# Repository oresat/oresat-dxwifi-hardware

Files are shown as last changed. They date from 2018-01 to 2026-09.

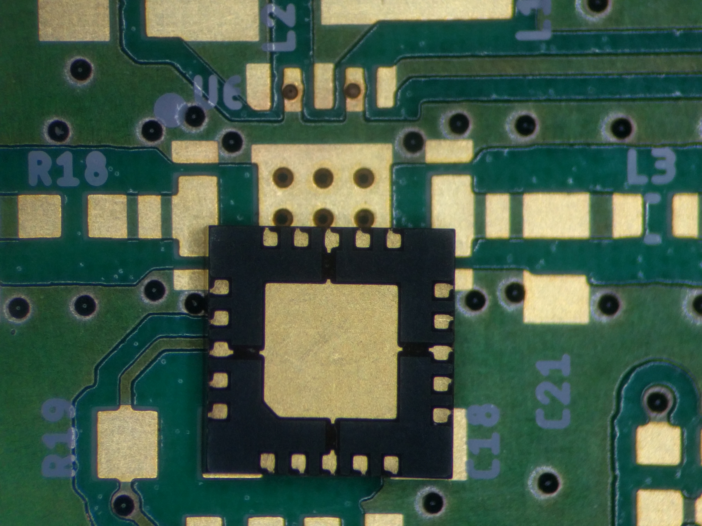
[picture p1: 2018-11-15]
bi-directional-amp-board_V2/v1_notes/IMG_20181114_184748.jpg

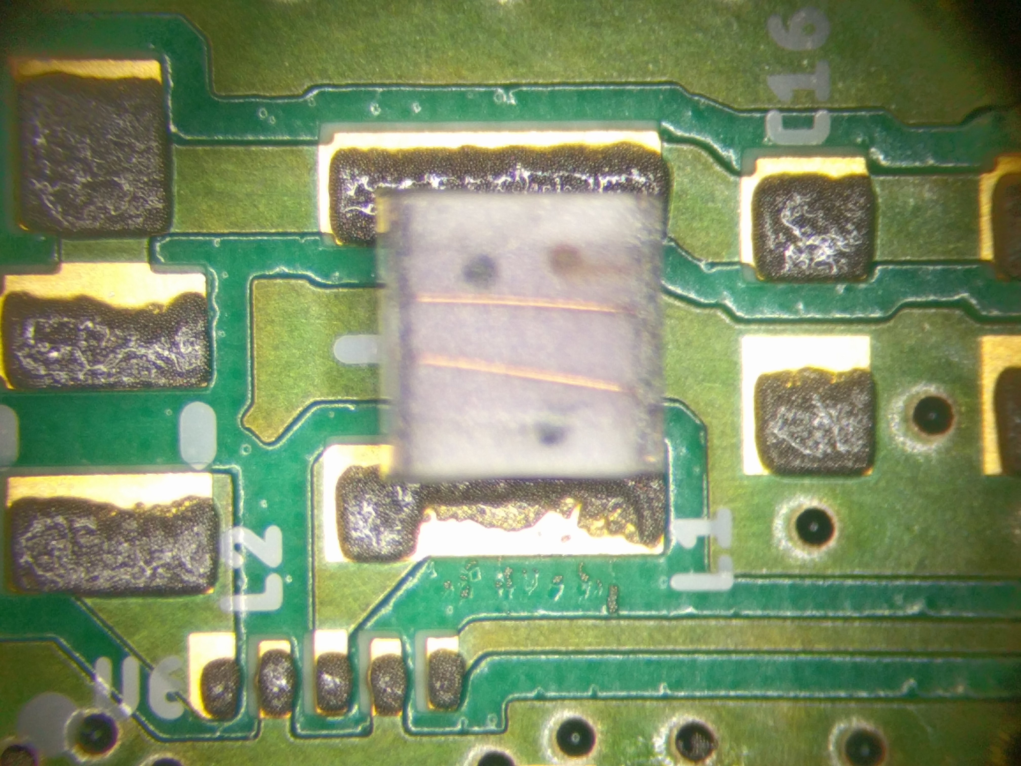
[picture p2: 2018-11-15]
bi-directional-amp-board_V2/v1_notes/IMG_20181114_191043.jpg

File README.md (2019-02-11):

# oresat-dxwifi-hardware
This repository is for the DxWiFi hardware that will fly on the OreSat satellite. DxWiFi is our communication subsystem for high speed data (1 Mbps) using 2.4 GHz WiFi between the spacecraft and ground.

This is hardware for the **satellite** only; please see the other repos if you're looking for the [OreSat Live Handheld Ground Station](https://github.com/oresat/oresat-live-handheld-ground-station) or the [Mini-OreSat testing platform for high altitude balloons](https://github.com/oresat/oresat-live-mini-oresat).

We intend to use "ordinary WiFi" (IEEE 802.11b) as a high speed satellite communication system. What is _not_ ordinary is that we run the radio under the amateur radio rules and regulations (FCC Part 97) and thus can increase power levels and antenna gains necessary to make the link budget work.

### Ordinary WiFi
The plan is to use the Qualcomm Atheros AR9271 USB to WiFi adapter because of the driver support in Linux.

### Non ordinary bi-directional power amplifier
This project is intended to operate under the Amateur Radio Service [47CFR97](https://www.gpo.gov/fdsys/pkg/CFR-1996-title47-vol5/pdf/CFR-1996-title47-vol5-part97.pdf) whereby larger power levels and higher gain directional antennas can be used within the [13 cm band](https://en.wikipedia.org/wiki/13-centimeter_band) to close the link.

NB:  There are other DxWiFi materials on the PSAS GitHub repo, but those repos are deprecated.

Link budgets can be found [here](https://github.com/oresat/oresat-dxwifi-hardware/tree/master/Link-Model).

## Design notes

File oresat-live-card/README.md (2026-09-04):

---
title: "**OreSat Live / DxWiFi Card**"
subtitle: |
  **Fabrication and Assembly Information**\
  For build TIME-STAMP
fontsize: 10pt
geometry:
  - margin=0.5in
toc: true
toc-depth: 2
colorlinks: true
urlcolor: blue
---

\newpage

# About this Board

## Board Description

TODO: DESCRIBE CARD

## Documentation Links

- OL hardware Git repository: <https://github.com/oresat/oresat-dxwifi-hardware>
- OL software Git reposity: <https://github.com/oresat/oresat-dxwifi-software>
- **TODO:** OL Design Notes + Design Review Notes

## Documentation Files

| Filename | Notes |
| --- | --- |
| README.pdf | This README file |
| PROJECT-NAME-outline.dxf | Board outline (with holes) in DXF format |
| PROJECT-NAME-pcba.step | 3D model of PCBA (with components) |
| PROJECT-NAME-render-bot.jpg | Render of the top of the 3D model |
| PROJECT-NAME-render-bot.jpg | Render of the bottom of the 3D model |
| PROJECT-NAME-schematic.pdf | PDF of board schematics |

## Contact Information

- Website: <https://www.oresat.org/>
- Email: <oresat@pdx.edu>
- Instagram: @pdxaerospace

## Board Renders

Render of the top of the 3D model
Render of the bottom of the 3D model

\newpage

# Printed Circuit Board (PCB) Fabrication Information

## Board Info

- 4 layer board
- Bounding box is 99.8 x 94.6 mm (3.93 x 3.72 in)
- Board thickness is 1.59 mm (0.063 inch)
- **Important:** See Materials and Stack Up sections below

## Board Requirements

- Design Rules
    - Minimum Trace / Space design rules
       - Outer layers: 0.127 mm (5.0 mil) / 0.127 mm (5.0 mil)
       - Inner layers: 0.127 mm (5.0 mil) / 0.127 mm (5.0 mil)
    - Outer dimension router tolerance: +/- 0.254 mm (10.0 mil)
    - Hole placement tolerance: +/- 0.075 mm (3.0 mil)
    - Inner tab routed slot tolerance: +/- 0.254 mm (10.0 mil)
- Drills
   - Drill Positional Tolerance: 0.051 mm (2.0 mil)
   - Drill Size tolerance: +/- 0.064 mm (2.5 mil)
- Plated/Un-plated holes
  - There are 6 un-plated (NPT) holes
  - There are 1477 plated through (PTH) holes
  - PTH minimum diameter: 0.254 mm (10 mil)
  - PTH minimum annulus: 0.102 mm (4 mil) radius
- Outline/Routing
  - Requires a 1.0 mm or smaller diameter routing bit
- Slots
  - There are no slots.
- Cutouts
  - There are no cutouts
- There are 3 fiducials on the top layer and 3 on the bottom layer.
- Panel tabs ("mouse bites")
   - Card edges must be smooth; no mouse bites or other intrusions into the card outline.
   - If external mouse bites are required, minimize and customer will remove by hand before assembly.
- If not otherwise specified, build to IPC 6012 Class 2 or better.

## Materials

- Controlled impedance
   - The stackup is critical for the performance of high speed signals on this board.
   - As long as the stackup is controlled, the board is not considered controlled impedance.
- Isola FR408HR or material with equivalent Dk.
- Board Surface treatment should be ENIG, althogh immersion Silver is acceptable.
- White silkscreen on top and bottom surface
- Taiyo PSR-4000 or equivalent soldermask on top and bottom, no requirements for color.

## Stack Up

| Layer | Thickness | Notes |
|---|---|---|
| Top Copper | 0.043 mm /  1.7 mil |  Layer 1 foil, 1 oz Cu after plating |
| prepreg | 0.200 mm /  7.9 mil |  Prepreg - Isola FR408HR 2113 |
| Layer 2 | 0.018 mm /  0.7 mil |  Layer 2 foil, 0.5 oz Cu |
| Core | 0.991 mm / 39 mil |  Core Isola FR408HR |
| Layer 3 | 0.018 mm /  0.7 mil |  Layer 3 foil, 0.5 oz Cu |
| prepreg | 0.200 mm /  7.9 mil |  Prepreg - Isola FR408HR 2113 |
| Bottom Copper | 0.043 mm /  1.7 mil |  Layer 4 foil, 1 oz copper after plating |
| **Total Stackup** | **1.588 mm / 62.5 mil** | |

## Array / Panel Information

- Coordinate with Contract Manufacturer (CM) for optimal size of this panel.
- If no feedback from CM, then produce single boards (no panel).

## Fabrication Files

### IPC-2581 File

| Filename | Notes |
| --- | --- |
| PROJECT-NAME-ipc2581.xml | IPC-2581 board information file |

### Legacy PCB Files

| Filename | Notes |
| ---| --- |
| PROJECT-NAME-Edge_Cuts.gbr | RS274X file for the dimension (outline) layer |
| PROJECT-NAME-F_Silkscreen.gbr | RS274X file for the top silkscreen |
| PROJECT-NAME-F_Mask.gbr | RS274X file for the top soldermask |
| PROJECT-NAME-F_Cu.gbr | RS274X file for the top copper layer |
| PROJECT-NAME-In1_Cu.gbr | RS274X file for the layer 2 copper |
| PROJECT-NAME-In2_Cu.gbr | RS274X file for the layer 3 copper |
| PROJECT-NAME-B_Cu.gbr | RS274X file for the bottom copper layer |
| PROJECT-NAME-B_Mask.gbr | RS274X file for the bottom soldermask |
| PROJECT-NAME-B_Silkscreen.gbr | RS274X file for the bottom silkscreen |
| PROJECT-NAME-NPTH.drl | Excellon file for non-plated through holes |
| PROJECT-NAME-PTH.drl | Excellon file for plated through holes | 

\newpage

# Printed Circuit Board Assembly (PCBA) Information

## Assembly Info

- There are components are on the top and bottom side of the board.
- This PCBA is mostly surface mount (SMT) with a few (THT) components.

## Assembly Requirements

- Assemble to IPC Class 2 or better
- Bake components that are not moisture sealed to appropriate levels as required.
- Solder paste MUST be leaded.
- Aqueous flux and wash strongly preferred.
   - Clean to NASA Standard "Visibly Clean (VC)": No particles or residues are visible to the naked eye.
- No conformal coating.
- Ship in antistatic protective bag

## Component Specific Assembly Information

- SMPM connectors (J3, J4) should be hand-added according to the Oresat SOP.

## Assembly Files

### IPC-2581 File

| Filename | Notes |
| --- | --- |
| PROJECT-NAME-ipc2581.xml | IPC-2581 board information file |

### Bill of Materials (BOM)

| Filename | Description |
| --- | --- |
| PROJECT-NAME-bom.csv | BOM in Comma Separated Variable format |

### Solder Paste Stencils

| Filename | Notes |
| --- | --- |
| PROJECT-NAME-B_Paste.gbr | RS274X file for top/front solder paste stencil |
| PROJECT-NAME-F_Paste.gbr | RS274X file for bottom/back solder paste stencil |

### Mounting/Placement Location

| Filename | Description |
| --- | --- |
| PROJECT-NAME-3u.pos | Pick and place locations for components |

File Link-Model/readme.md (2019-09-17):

### Link Budget Models for the DxWiFi Channel

The source of these link model spreadsheets are from Jan King and are located at the [AMSAT-UK IARU website](http://www.amsatuk.me.uk/iaru/spreadsheet.htm).  The spreadsheets have been customized from revision 2.5.5 which are signified by a suffix letter.  In addition, for OreSat protocol information please visit our [GitHub protocol page](https://github.com/oresat/oresat-design/tree/gh-pages/protocol).  For OreSat's primary communication link models please visit our [GitHub C3 RF page](https://github.com/oresat/oresat-c3-rf/link-models)

* The bulk-data mission uplink and downlink using UniClOGS (University Class Open Ground Station)
  * ___OreSat1_link_model_v2.5.5a_mission_data_uniclogs.xlsx  (PDF summary)___
  * S band - 2422 MHz - 1Mbps 802.11b
  * 45 deg minimum elevation
  * 1.4 dBi canted turnstile on satellite and 23 dBi parabolic reflector at ground station for uplink
  * 12 dBi helix on satellite and 23 dBi parabolic reflector at ground station for downlink

* The bulk-data mission downlink using a handheld ground station receiver
  * ___OreSat1_link_model_v2.5.5a_mission_data_handheld.xlsx  (PDF summary)___
  * S band - 2422 MHz - 1Mbps 802.11b
  * 45 deg minimum elevation
  * 12 dBi helix on satellite and 15 dBi quad helix/patch at ground station

Notes:
- The 'Transmitters' and 'Receivers' sheets have been customized
  - Block diagrams reflect correct design
  - System noise temperature is more precise
- The 'System Performance Summary' sheet has been customized
  - Power levels in dBm
  - More link details

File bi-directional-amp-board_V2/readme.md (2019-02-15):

Notes on the Bi-Directional DxWiFi (2.412 GHz) Amp PCB
========================================================

Our stackup is something like this:

 1.2 mil - 1 oz Copper
13.3 mil - Rogers RO4350B
 1.2 mil - 1 oz Copper
31.1 mil - FR4 (e.g., NP175)
 1.2 mil - 1 oz Copper
13.3 mil - Rogers RO4350B
 1.2 mil - 1 oz Copper
--------
62.5 mil - 1/16" standard board thickness

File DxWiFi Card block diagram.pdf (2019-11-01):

To Helix
Antenna

To Turnstile
Antenna

WiFi Adapter
TX Port

WiFi Adapter
RX Port

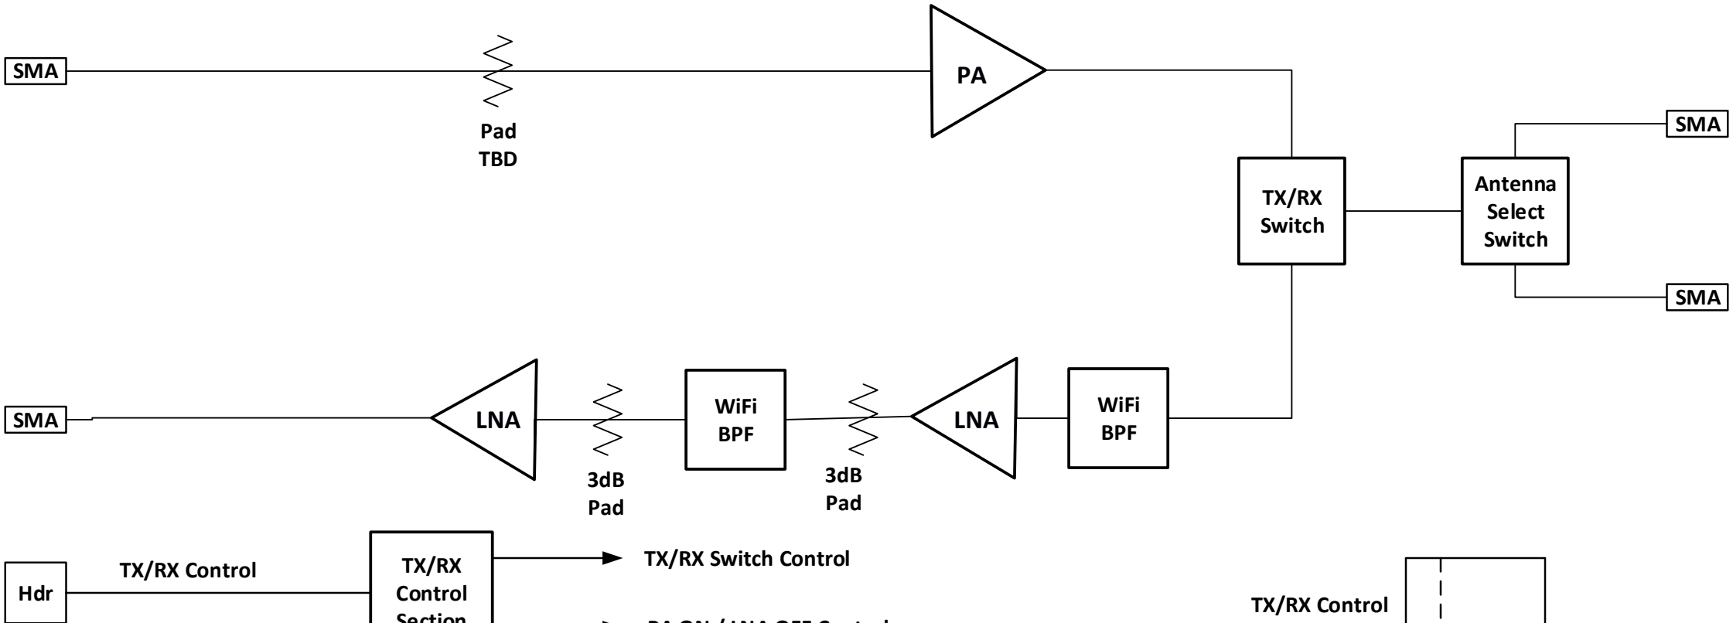
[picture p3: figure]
TX/RX Switch; Antenna Select Switch; WiFi BPF; WiFi; BPF LNA; LNA; 3dB Pad; SMA; Pad TBD; TX/RX Control; Hdr; TX/RX Switch Control

Section

Hdr

Hdr

Antenna Select Switch Control

PA ON / LNA OFF Control

Helix/Turnstile Select

+5VDC
To All Loads

WiFi Adapter
TX On

Pocket Beagle
(or jumper select)

Lab Supply

## DxWiFi Amplifier Board Version 2 Simplified Block Diagram

ojones
11/1/19
10uS | 10uS

TX/RX Switch Control

PA ON / LNA OFF Control

TX/RX Timing Diagram

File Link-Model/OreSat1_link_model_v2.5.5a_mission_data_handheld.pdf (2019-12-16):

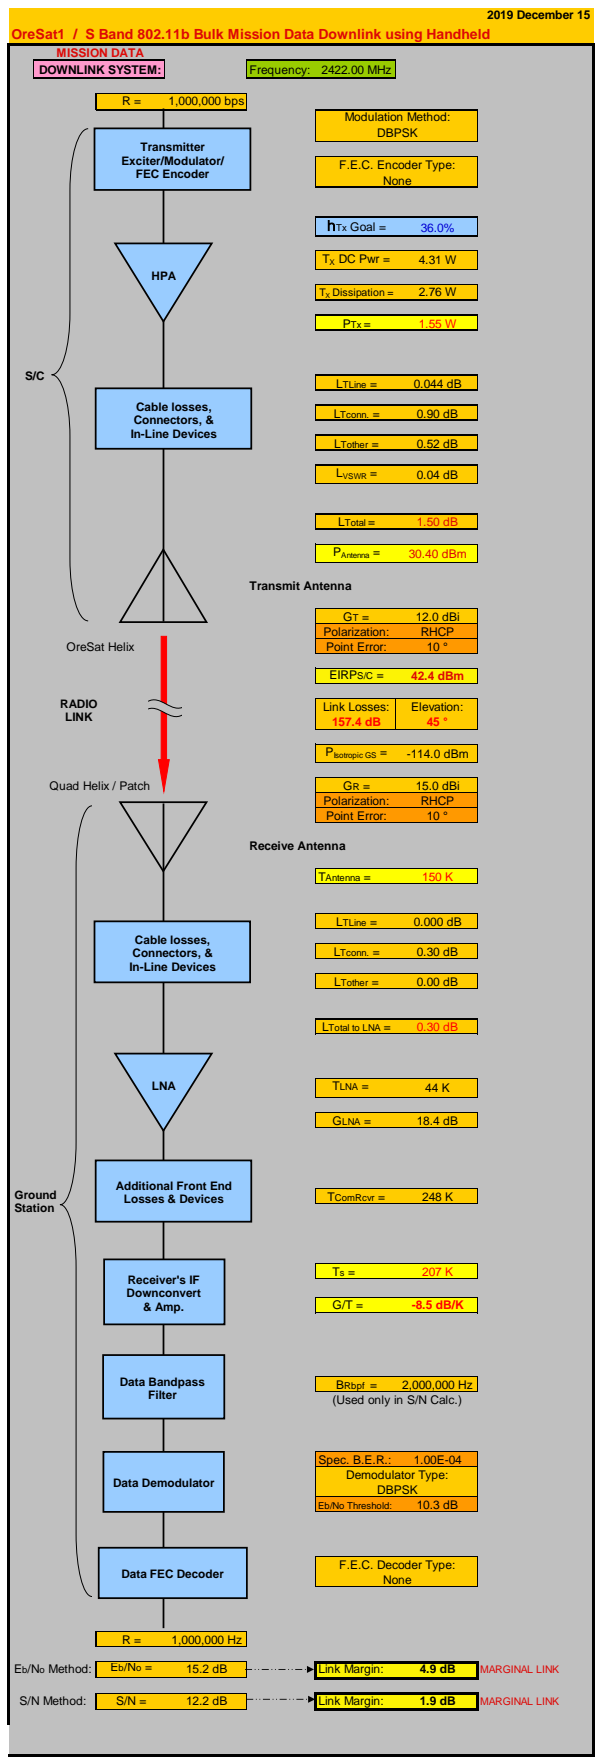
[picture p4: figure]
2019 December 15; Frequency: 2422.00 MHz; 1,000,000 bps; hTx Goal =; TX DC Pwr =; TX Dissipation =; PTx =; LTLine =; LTconn. =; LTother =; LVSWR =; LTotal =; PAntenna =; 30.40 dBm; Transmit Antenna; 12.0 dBi; Polarization:; RHCP; Point Error:; EIRPS/C =; 42.4 dBm; Link Losses:; Elevation:; PIsotropic GS =; -114.0 dBm; 15.0 dBi; Receive Antenna; TAntenna =; LTotal to LNA =; TLNA =; GLNA =; TComRcvr =; BRbpf =; Spec. B.E.R.:; Eb/No Threshold:; Link Margin:; MARGINAL LINK; DBPSK; MISSION DATA; DOWNLINK SYSTEM:; Modulation Method:; F.E.C. Encoder Type: None; OreSat Helix; Quad Helix / Patch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

### OreSat1 / S Band 802.11b Bulk Mission Data Downlink using Handheld

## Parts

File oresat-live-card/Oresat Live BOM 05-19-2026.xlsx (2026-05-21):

Qty | Reference | Value | MFR | MPN | Description | DIS | DPN | ALT DIS | ALT DPN
49 | C1,C3,C4,C7,C11,C15,C16,C18,C20,C21,C23,C26,C28,C31,C36,C38,C39,C41,C42,C43,C45,C46,C47,C54,C55,C56,C57,C58,C59,C60,C65,C66,C67,C68,C70,C71,C72,C74,C77,C86,C87,C88,C89,C98,C99,C105,C106,C111,C118 | 100n | TDK Corporation | CGA3E2X7R1E104K080AA | CAP CER 0.1UF 25V X7R 0603 | DigiKey | 445-5667-1-ND
1 | C110 | 1p | Murata Electronics | GCM1555C1H1R0CA16J | CAP CER 1PF 50V C0G/NP0 0402 | DigiKey | 490-17745-1-ND
2 | C112,C113 | 100n | TDK Corporation | CGA2B3X7R1E104K050BB | CAP CER 0.1UF 25V X7R 0402 | DigiKey | 445-6902-1-ND
9 | C13,C14,C40,C79,C80,C81,C82,C83,C95 | 22u | TDK Corporation | CGA6P1X7R1C226M250AC | CAP CER 22UF 16V X7R 1210 | DigiKey | 445-5723-1-ND
2 | C17,C37 | 2u2 | Murata Electronics | GRM188Z71C225ME43J | CAP CER 2.2UF 16V X7R 0603 | DigiKey | 490-GRM188Z71C225ME43JCT-ND
6 | C19,C22,C29,C30,C63,C64 | 12p | TDK Corporation | CGA3E2C0G1H120J080AA | CAP CER 12PF 50V C0G 0603 | DigiKey | 445-5629-1-ND
8 | C2,C8,C27,C44,C53,C69,C75,C76 | 10u | TDK Corporation | CGA4J1X7S1C106M125AC | CAP CER 10UF 16V X7S 0805 | DigiKey | 445-16111-1-ND
10 | C24,C49,C94,C103,C104,C107,C114,C115,C116,C117 | 100p | Murata Electronics | GCM1555C1H101GA16D | CAP CER 100PF 50V C0G/NP0 0402 | DigiKey | 490-GCM1555C1H101GA16DCT-ND
2 | C32,C35 | 1u | TDK Corporation | CGA4J2X7R1C105K125AA | CAP CER 1UF 16V X7R 0805 | DigiKey | 445-5689-1-ND
3 | C48,C108,C109 | 1n | TDK Corporation | CGA2B2NP01H102J050BA | CAP CER 1000PF 50V NP0 0402 | DigiKey | 445-12118-1-ND
13 | C5,C6,C9,C10,C12,C33,C34,C61,C62,C73,C78,C84,C85 | 1u | TDK Corporation | CGA3E1X7R1C105K080AC | CAP CER 1UF 16V X7R 0603 | DigiKey | 445-12539-1-ND
1 | C50 | 3p | KYOCERA AVX | 04025U3R0BAT2A | CAP CER 3PF 50V NP0 0402 | Mouser | 581-04025U3R0BAT2A
1 | C51 | 1.4p | KYOCERA AVX | 04025J1R4PBSTR\500 | CAP 50V 1.4pF .02pFTol ThinFilm 0402 | Mouser | 581-04025J1R4PBSTR5
1 | C52 | 1.6p | KYOCERA AVX | 04025U1R6BAT2A | CAP CER 1.6PF 50V NP0 0402 | Mouser | 581-04025U1R6BAT2A
3 | C90,C91,C93 | 15p | Murata Electronics | GJM1555C1H150JB01D | CAP CER 15PF 50V C0G/NP0 0402 | DigiKey | 490-3117-1-ND
1 | C92 | 1u | Taiyo Yuden | EMK105BJ105KVHF | CAP CER 1UF 16V X5R 0402 | DigiKey | 587-3709-1-ND
8 | D1,D6,D7,D8,D9,D10,D11,D15 | GRN | Würth Elektronik | 150060GS75020 | Green 525nm LED 3.2V 0603 | DigiKey | 732-150060GS75020CT-ND
4 | D2,D3,D4,D5 | BLUE | Würth Elektronik | 150060BS75020 | Blue 470nm LED 3.2V 0603 | DigiKey | 732-150060BS75020CT-ND
3 | FB1,FB2,FB3 | BLM18KG300TH1D | Murata Electronics | BLM18KG300JH1D | FERRITE BEAD 30 OHM 0603 1 LN | DigiKey | 490-13263-1-ND
2 | FB4,FB5 | MMZ1608Y221BTD25 | TDK Corporation | MMZ1608Y221BTD25 | FERRITE BEAD 220 OHM 0603 1LN | DigiKey | 445-MMZ1608Y221BTD25CT-ND
2 | FL1,FL2 | QPQ1907SR | Qorvo | QPQ1907SR | 2.4GHZ WI-FI LTE COEXBOOST BAW F | DigiKey | 2312-QPQ1907SRCT-ND
1 | J1 | ORESAT-DEBUG-CONNECTOR | TE Connectivity AMP Connectors | 2-1734592-0 | CONN FPC BOTTOM 20POS 0.50MM R/A | DigiKey | A100287CT-ND | Mouser | 571-2-1734592-0
2 | J11,J15 | 2X1_TH_JUMPER
1 | J14 | Conn_01x02 |  |  | Generic connector, single row, 01x02, script generated (kicad-library-utils/schlib/autogen/connector/)
2 | J2,J10 | SM06B-SRSS-TB | JST Commercial | SM06B-SRSS-TB | CONN HEADER SMD R/A 6POS 1MM | DigiKey | 455-SM06B-SRSS-TBCT-ND
1 | J4 | TFM-120-01-L-D-RA | Samtec Inc. | TFM-120-01-L-D-RA | CONN HEADER R/A 40POS 1.27MM | DigiKey | On Reels
2 | J6,J8 | SMPM | TE Connectivity Linx | 2477330-1 | CONN SMPM PLUG STR 50OHM EDGEMNT | DigiKey | 343-2477330-1CT-ND
1 | J7 | DM3BT-DSF-PEJS | Hirose Electric Co Ltd | DM3BT-DSF-PEJS | CONN MICRO SD CARD R/A SMD | DigiKey | HR1942CT-ND
2 | J9,J12 | U.FL | Hirose Electric Co Ltd | U.FL-R-SMT-1(10) | CONN U.FL RCPT STR 50 OHM SMD | DigiKey | H11891CT-ND
2 | L1,L2 | 3u3 | Coilcraft | XGL4020-332MEC | FIXED IND 3.3UH 6.6A 34MOHM SMD | DigiKey | 2457-XGL4020-332MEC-ND
1 | L10 | 10n | Coilcraft | 1008HQ-10NXJLC | Fixed Inductors 1008 10nH Unshld 5% | Coilcraft | 1008HQ-10NXJLC
1 | L3 | 18nH | Coilcraft | 0603DC-18NXJRW | FIXED IND 18NH 2A 78 MOHM SMD | DigiKey | 2457-0603DC-18NXJRW-ND | Mouser | 994-0603DC-18NXJRW
1 | L4 | 1.5n | Delta Electronics/Components | 0402HM-1N5EKTS | FIXED IND 1.5NH 1A 30 MOHM SMD | DigiKey | 2035-1382-1-ND
1 | L7 | 1.7n | Coilcraft | 0402DC-1N7XJRW | 1.7nH RF Inductor, ceramic core, 5% tol | DigiKey | 2457-0402DC-1N7XJRW-ND | Mouser | 994-0402DC-1N7XJRW
1 | L8 | 6.8n. | Coilcraft | 0805CS-060XJRC | FIXED IND 6.8NH 600MA 110MOHM SM | DigiKey | 2457-0805CS-060XJRC-ND
1 | L9 | 1.0n | TDK Corporation | MLK1005S1N0ST000 | FIXED IND 1NH 500MA 100 MOHM SMD | DigiKey | 445-MLK1005S1N0ST000CT-ND
1 | PCB1 | ORESAT-CARD-V1.3-GENERIC-1RF-POS1 | N/A | N/A | N/A | N/A | N/A
1 | PCBA1 | WF-NP9202WF | Unknown | Unknown | AR9271 USB to WiFi daughter board | N/A | N/A
1 | Q1 | PMMBT2907A | Nexperia USA Inc. | PMBT2907A,215 | TRANS PNP 60V 0.6A TO-236AB | DigiKey | 1727-2958-1-ND | Mouser | 771-PMBT2907T/R
2 | Q2,Q4 | DMN3028 | Diodes Incorporated | DMN3028LQ-7 | MOSFET BVDSS: 25V~30V,SOT23 | DigiKey | 31-DMN3028LQ-7CT-ND
1 | Q3 | DMP2240UDM | Diodes Incorporated | DMP2240UDM-7 | Dual PMOS transistor, 6 pin package | DigiKey | DMP2240UDMDICT-ND
2 | Q5,Q6 | DMPH2040 | Diodes Incorporated | DMPH2040UVTQ-7 | MOSFET P-CH 20V 5.6/11.7A TSOT26 | DigiKey | 31-DMPH2040UVTQ-7CT-ND
12 | R1,R2,R3,R4,R5,R20,R22,R29,R30,R49,R51,R85 | 4.7k | Panasonic | ERJ-3EKF4701V | RES SMD 4.7K OHM 1% 1/10W 0603 | DigiKey | P4.70KHCT-ND
1 | R105 | 33k | Panasonic | ERJ-U03F3302V | RES 33K OHM 1% 1/10W 0603 | DigiKey | 10-ERJ-U03F3302VCT-ND
1 | R106 | 0 | Panasonic | ERJ-2GE0R00X | RES SMD 0 OHM JUMPER 1/10W 0402 | DigiKey | P0.0JCT-ND
1 | R109 | 56 | Panasonic | ERJ-3EKF56R0V | RES SMD 56 OHM 1% 1/10W 0603 | DigiKey | P56.0HCT-ND
5 | R11,R12,R14,R19,R33 | 100k | Panasonic | ERJ-3EKF1003V | RES SMD 100K OHM 1% 1/10W 0603 | DigiKey | P100KHCT-ND
2 | R115,R123 | 5.62k | Panasonic | ERJ-3EKF5621V | RES SMD 5.62K OHM 1% 1/10W 0603 | DigiKey | P5.62KHCT-ND
2 | R116,R124 | 5.62k | Panasonic | ERJ-2RKF5621X | RES SMD 5.62K OHM 1% 1/10W 0402 | DigiKey | P5.62KLCT-ND
2 | R117,R125 | 10k | Panasonic | ERJ-2RKF1002X | RES SMD 10K OHM 1% 1/10W 0402 | DigiKey | P10.0KLCT-ND
3 | R118,R119,R120 | 4.99k | Panasonic | ERJ-3EKF4991V | RES SMD 4.99K OHM 1% 1/10W 0603 | DigiKey | P4.99KHCT-ND
3 | R13,R36,R44 | 1M | Panasonic | ERJ-3EKF1004V | RES SMD 1M OHM 1% 1/10W 0603 | DigiKey | P1.00MHCT-ND
1 | R23 | 499 | Panasonic | ERJ-3EKF4990V | RES SMD 499 OHM 1% 1/10W 0603 | DigiKey | P499HCT-ND
3 | R24,R25,R26 | 100k | Panasonic | EXB-A10P104J | RES ARRAY 8 RES 100K OHM 2512 | DigiKey | U7104CT-ND
1 | R31 | 40.2K | Panasonic | ERJ-3EKF4022V | RES SMD 40.2K OHM 1% 1/10W 0603 | DigiKey | P40.2KHCT-ND
2 | R35,R43 | 665k | Panasonic | ERJ-3EKF6653V | RES SMD 665K OHM 1% 1/10W 0603 | DigiKey | P665KHCT-ND
2 | R37,R45 | 330k | Panasonic | ERJ-3EKF3303V | RES SMD 330K OHM 1% 1/10W 0603 | DigiKey | P330KHCT-ND
6 | R41,R48,R71,R92,R93,R121 | 100 | Panasonic | ERJ-3EKF1000V | RES SMD 100 OHM 1% 1/10W 0603 | DigiKey | P100HCT-ND
8 | R47,R59,R60,R94,R96,R98,R99,R100 | 0 | Panasonic | ERJ-3GEY0R00V | RES SMD 0 OHM JUMPER 1/10W 0603 | DigiKey | P0.0GCT-ND
6 | R54,R55,R57,R95,R103,R107 | 1k | Panasonic | ERJ-3EKF1001V | RES SMD 1K OHM 1% 1/10W 0603 | DigiKey | P1.00KHCT-ND
33 | R6,R7,R15,R16,R17,R18,R21,R28,R32,R34,R38,R39,R40,R46,R50,R52,R61,R62,R64,R72,R74,R75,R76,R77,R79,R88,R89,R90,R91,R104,R108,R114,R122 | 10k | Panasonic | ERJ-3EKF1002V | RES SMD 10K OHM 1% 1/10W 0603 | DigiKey | P10.0KHCT-ND
1 | R63 | 100m | Panasonic | ERJ-8BWFR100V | RES 0.1 OHM 1% 1W 1206 | DigiKey | P.10AUCT-ND
1 | R78 | 9.53k | Panasonic | ERJ-3EKF9531V | RES 9.53K OHM 1% 1/10W 0603 | DigiKey | P9.53KHCT-ND
3 | R8,R9,R10 | 10k | Panasonic | EXB-A10P103J | RES ARRAY 8 RES 10K OHM 2512 | DigiKey | U7103CT-ND
1 | R80 | 0 | Panasonic | ERJ-6GEY0R00V | RES SMD 0 OHM JUMPER 1/8W 0805 | DigiKey | P0.0ACT-ND
1 | R81 | 110 | Panasonic | ERJ-2RKF1100X | RES SMD 110 OHM 1% 1/10W 0402 | DigiKey | P110LCT-ND
1 | R82 | 220 | Panasonic | ERJ-3EKF2200V | RES SMD 220 OHM 1% 1/10W 0603 | DigiKey | P220HCT-ND
1 | R83 | 90.9k | Panasonic | ERJ-3EKF9092V | RES SMD 90.9K OHM 1% 1/10W 0603 | DigiKey | P90.9KHCT-ND
1 | R84 | 3.3 | Vishay Dale | CRCW04023R30FKED | RES SMD 3.3 OHM 1% 1/16W 0402 | DigiKey | 541-3.30LLCT-ND
2 | R86,R87 | 499K | Panasonic | ERJ-U03F4993V | RES 499K OHM 1% 1/10W 0603 | DigiKey | 10-ERJ-U03F4993VCT-ND
1 | RT1 | TDK NTCG163JX103DT1S | TDK Corporation | NTCG163JX103DT1S | THERMISTOR NTC 10KOHM 3380K 0603 | DigiKey | 445-174518-1-ND
1 | U1 | RCLAMP0504FB | Semtech Corporation | RCLAMP0504FBTCT | TVS DIODE 5V 17.5V SC70-6 | DigiKey | RCLAMP0504FBTCTCT-ND
1 | U10 | TLVH431 | Texas Instruments | TLVH431BQDBZRQ1 | IC VREF SHUNT ADJ 0.5% SOT23-3 | DigiKey | 296-36778-1-ND
1 | U11 | TCAN330G | Texas Instruments | TCAN330GDCNR | High-Speed CAN Transceiver, 1Mbps, 3.3V supply, silent mode, shutdown mode, SOT-23-8/SOIC-8 | DigiKey | 296-TCAN330GDCNRCT-ND
2 | U12,U13 | MIC842LYC5 | Microchip Technology | MIC842LYC5-TR | IC Single Comparator W/REF, SC-70-5 | DigiKey | 576-2927-1-ND
1 | U14 | MAX4211 | Maxim Integrated | MAX4211FETE+ | IC CURRENT MONITOR 1.5% 16TQFN | DigiKey | MAX4211FETE+-ND
1 | U16 | MAX7310 | Maxim Integrated | MAX7310ATE+ | I2C 8-Bit GPIO Expander, 16-TQFN | DigiKey | MAX7310ATE+-ND
2 | U17,U27 | PAT1220-C-3DB | Susumu | PAT1220-C-3DB-T5 | RF ATTENUATOR 3DB 50OHM 0805 | DigiKey | PAT123CT-ND | Newark | 72AK4953
1 | U18 | TQP3M9037 | Qorvo | TQP3M9037 | LOW NOISE AMPLIFIER | DigiKey | 2312-TQP3M9037CT-ND
1 | U19 | TQP9111 | Qorvo | TQP9111 | 1800-2700 MHZ, 2 W HIGH GAIN AMP | DigiKey | 2312-TQP9111CT-ND
1 | U2 | TUSB4020BI | Texas Instruments | TUSB4020BIPHPRQ1 | 2-Port USB 2.0 Hub | DigiKey | 296-43165-1-ND
1 | U21 | TLV73311 | Texas Instruments | TLV73311PDBVR | IC REG LINEAR 1.1V 300MA SOT23-5 | DigiKey | 296-40663-1-ND
1 | U22 | TS5A21366 | Texas Instruments | TS5A21366DCUR | IC SWITCH SPST-NOX2 1OHM 8VSSOP | DigiKey | 296-24304-1-ND
2 | U24,U25 | LTC6994-1 | Analog Devices | LTC6994IS6-1#TRPBF | TimerBlox Delay Block | DigiKey | 584-C6994IS6-1TRPBF
2 | U26,U35 | SN74LVC1G32QDBVRQ1 | Texas Instruments | SN74LVC1G32QDBVRQ1 | IC GATE OR 1CH 2-INP SOT23-5,Single OR Gate, Low-Voltage CMOS | DigiKey | 296-24202-1-ND
1 | U28 | PD2328J5050S2HF | ANAREN | PD2328J5050S2HF | Power Divider 50ohm 2300 - 2800 MHz | DigiKey | 1173-1098-1-ND
1 | U29 | LT5538 | Analog Devices | LT5538IDD#TRPBF | IC RF DETECT 40MHZ-3.8GHZ 8DFN | DigiKey | LT5538IDD#TRPBFCT-ND
1 | U3 | MTFC32GAZAQHD-IT | Micron Technology Inc. | MTFC32GAZAQHD-IT | IC FLASH 256GBIT EMMC 153VFBGA | Mouser | 340-505444-TRAY
2 | U30,U32 | SN74LV1T34 | Texas Instruments | SN74LV1T34QDCKRQ1 | IC BUFF NON-INVERT 5.5V SC-70-5 | DigiKey | 296-SN74LV1T34QDCKRQ1CT-ND
2 | U34,U36 | QPC1022 | Qorvo | QPC1022TR7 | 5-6000 MHZ LOW DISTORTION SPDT S | DigiKey | 2312-QPC1022TR7CT-ND
1 | U4 | SN74AUC1G07DCKR | Texas Instruments | SN74AUC1G07DCKR | IC BUFF NON-INVERT 2.7V SC-70-5 | DigiKey | 296-12464-1-ND
2 | U5,U15 | LTC3624-5 | Analog Devices | LTC3624IDD-5#PBF | IC REG BUCK 5V 2A 8DFN | DigiKey | LTC3624IDD-5#PBF-ND
1 | U6 | SN74LVC1G04DCKR | Texas Instruments | SN74LVC1G04DCKR | IC INVERTER 1CH 1-INP SC70-5 | DigiKey | 296-11600-1-ND
1 | U7 | OSD3358 | Octavo Systems | OSD3358-1G-ISM | IC MODULE CORTEX-A8 1GHZ 1GB | DigiKey | 1676-OSD3358-1G-ISM-ND
1 | U8 | MIC94070YC6-TR | Microchip Technology | MIC94070YC6-TR | IC PWR SWITCH P-CHAN 1:1 SC70-6 | DigiKey | 576-3006-1-ND
2 | U9,U20 | TPS2041BQDBVRQ1 | Texas Instruments | TPS2041BQDBVRQ1 | Power Switch/Driver 1:1 N-Channel 500mA | DigiKey | 296-25159-1-ND
2 | Y1,Y3 | 24MHz | ECS Inc. | ECS-240-12-30BQ-AEN-TR | CRYSTAL 24.0000MHZ 12PF SMD | DigiKey | XC2580CT-ND
1 | Y2 | 32.768KHZ | Abracon LLC | ABS07-32.768KHZ-T | CRYSTAL 32.7680KHZ 12.5PF SMD | DigiKey | 535-9542-1-ND

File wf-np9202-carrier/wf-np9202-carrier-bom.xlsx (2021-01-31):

Qty | Refs | MFR | MPN | Value | DESCRIPTION | DIST | DPN
2 | ANT1,ANT2 | Yageo | ANTX100P001B24003 | N/A | 2.45GHz Bluetooth, Wi-Fi, Zigbee™ PCB Trace RF Antenna 2.4GHz ~ 2.5GHz 4.4dBi U.FL (UMCC), IPEX MHF1 Adhesive | Digi-Key | 311-4609-ND
1 | C20 | AVX Corporation | 0603YC105JAT2A | 1 uF | 1µF ±5% 16V Ceramic Capacitor X7R 0603 (1608 Metric) | Digi-Key | 478-10814-1-ND
1 | C9 | AVX Corporation | 06031C101JAT2A | 100pF | 100pF ±5% 100V Ceramic Capacitor X7R 0603 (1608 Metric) | Digi-Key | 478-12671-1-ND
1 | CABLE1 | JST Sales America Inc. | A06SR06SR30K51A | N/A | 6 Position Cable Assembly Rectangular Socket to Socket, Reversed 0.167' (50.80mm, 2.00") | Digi-Key | 455-2999-ND
1 | E5 | Murata Electronics | BLM18GG471SZ1D | N/A | 470 Ohms @ 100MHz 1 Signal Line Ferrite Bead 0603 (1608 Metric) 200mA 1.3Ohm | Digi-Key | 490-16658-1-ND
1 | J1 | CUI Devices | UJ2-MIBH2-4-SMT-TR | N/A | USB - micro B USB 2.0 Receptacle Connector 5 Position Surface Mount, Right Angle; Through Hole | Digi-Key | 102-4007-1-ND
1 | J3 | JST Sales America Inc. | SM06B-SRSS-TB(LF)(SN) | N/A | Connector Header Surface Mount, Right Angle 6 position 0.039" (1.00mm) | Digi-Key | 455-1806-1-ND
2 | LED1, LED2 | Lite-On | LTST-C193KGKT-5A | N/A | Green 572nm LED Indication - Discrete 2V 0603 (1608 Metric) | Digi-Key | 160-1828-1-ND
1 | PCBA1 | ?? | WF-NP9202 v1.0 | N/A | AR9271-based USB to 802.11bgn module | AliExpress | WF-NP9202
1 | R1 | Rohm Semiconductor | SFR03EZPJ000 | 0 | 0 Ohms Jumper 0.1W, 1/10W Chip Resistor 0603 (1608 Metric) Anti-Sulfur Thick Film | Digi-Key | 511-1823-1-ND
3 | R6, R7, R9 | Rohm Semiconductor | SFR03EZPF1001 | 1k | 1 kOhms ±1% 0.1W, 1/10W Chip Resistor 0603 (1608 Metric) Anti-Sulfur Thick Film | Digi-Key | 511-1818-1-ND

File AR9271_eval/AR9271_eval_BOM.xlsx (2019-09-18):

Bill Of Materials for AR9721
Source file: AR9721_eval.sch
Last modified: 2019/09/17
PCB version: 1.0 |  |  | P/DNP = | Place/Do Not Place (DNP is for final production boards)
BOM revision: 0 |  |  | Generic = | Any generic part with the same characteristics are OK (e.g., bypass cap)
Cnt | Part References | P/DNP | Mfg | Mfg PN | Description | Generic | Dist | Dist Part Number
9 | C1, C22, C24, C25, C46, C47, C49, C50, C53 | P | Murata Electronics | GCM31CR71C475KA37L | Capacitor, 4.7uF, 1206 | Y | Digi-key | 490-6065-1-ND
4 | C10, C11, C12, C13 | P | Taiyo Yuden | UMK063CG020CTHF | Capacitor, 2pF, 0201 | Y | Digi-key | 587-3777-2-ND
2 | C14, C19 | P | Taiyo Yuden | UMK063CG010CTHF | Capacitor, 1pF, 0201 | Y | Digi-key | 587-3776-1-ND
2 | C17, C18 | P | Taiyo Yuden | UMK063CG1R5CT-F | Capacitor, 1.5pF, 0201 | Y | Digi-key | 587-3202-6-ND
15 | C2, C3, C6, C26, C27, C28, C29, C30, C31, C32, C33, C34, C43, C45, C51 | P | TDK | CGA2B1X7R1C104K050BC | Capacitor, 100nF, 0402 | Y | Digi-key | 445-5613-1-ND
1 | C21 | P | Taiyo Yuden | UMK063CG101JT-F | Capacitor, 100pF, 0201 | Y | Digi-key | 587-3207-2-ND
4 | C23, C39, C44, C48 | P | Kemet | C0402C103K4RACAUTO | Capacitor, 10nF, 0402 | Y | Digi-key | 399-6825-1-ND
1 | C37 | P | TDK | CGA2B2C0G1H101J050BA | Capacitor, 100pF, 0402 | Y | Digi-key | 445-5596-1-ND
2 | C38, C40 | P | Kemet | C0402C102K5GACTU | Capacitor, 1nF, 0402 | Y | Digi-key | 399-7756-1-ND
4 | C4, C5, C35, C36 | P | Yageo | CC0402JRNPO9BN100 | Capacitor, 10pF, 0402 | Y | Digi-key | 311-1014-1-ND
3 | C41, C42, C52 | P | TDK | CGA2B2C0G1H100D050BA | Capacitor, 1uF, 0402 | Y | Digi-key | 445-5584-1-ND
1 | C7 | P | Taiyo Yuden | UMK063CG2R2CTHF | Capacitor, 2.2pF, 0201 | Y | Digi-key | 587-5314-1-ND
5 | C8, C9, C15, C16, C20 | P | Taiyo Yuden | UMK063CG100DTHF | Capacitor, 10pF, 0201 | Y | Digi-key | 587-3785-2-ND
1 | D1 | P | Skyworks | SMP1321-079 | RF PIN Diode | N | Digi-key | 863-1099-1-ND
2 | D2, D3 | P | Littelfuse Inc. | PGB1010603MR | PGB1 Series 15 V 63 Bi-Directional SMT ESD TVS | Y | Digi-key | F2594CT-ND
1 | J1 | P | CUI Inc. | UJ2-MIBH2-4-SMT-TR | Micro B Type 5 Pin Horizontal SMT USB Jack 2.0 | Y | Digi-key | 102-4007-1-ND
1 | J3 | P | Samtec Inc. | HTST-110-01-L-DV-P | Conn Shrouded Header HDR 20 POS 2.54mm Solder ST SMD | Y | Digi-key | SAM15675-ND
2 | J7, J8 | P | Amphenol RF | 132134-15 | Rf Coaxial, Sma, Straight Jack, Pcb | Y | Digi-key | ACX1962-ND
4 | JP1, JP2, JP3, JP4 | P | NA | NA | PIN HEADER | Y | Digi-key | 952-3308-ND
2 | L1, L2 | P | Murata Electronics | LQP03TN1N8B02D | Inductor, 1.8nH, 0201 | Y | Digi-key | 490-6720-1-ND
2 | L3, L4 | P | Murata Electronics | LQP03TN2N2B02D | Inductor, 2.2nH, 0201 | Y | Digi-key | 490-6723-1-ND
1 | L5 | P | Murata Electronics | BLM18PG221SH1D | FERRITE BEAD 220 OHM 0603 1LN | N | Digi-key | 490-7817-1-ND
12 | LED1, LED2, LED3, LED4, LED5, LED6, LED7, LED8, LED9, LED10, LED11, LED12 | P | Lite-On | LTST-C193KGKT-5A | LED,Green,0603, | Y | Digi-key | 160-1828-1-ND
3 | R1, R36, R37 | NP | NA | NA | NA | NA | NA | NA
12 | R11, R15, R16, R17, R18, R19, R20, R21, R22, R23, R24, R25 | P | Panasonic | ERJ-2GEJ511X | Resistor, 510, 0402 | Y | Digi-key | P510JTR-ND
1 | R12 | P | Panasonic | ERJ-2GEJ330X | Resistor, 33, 0402 | Y | Digi-key | P33JCT-ND
2 | R2, R3 | P | Panasonic | ERJ-2GE0R00X | Resistor, 0, 0402 | Y | Digi-key | P0.0JCT-ND
1 | R26 | P | Panasonic | ERJ-1GNF1001C | Resistor, 1k, 0201 | Y | Digi-key | P122413CT-ND
2 | R27, R30 | P | Panasonic | ERJ-2RKF3303X | Resistor, 330k, 0402 | Y | Digi-key | P330KLCT-ND
2 | R28, R31 | P | Panasonic | ERJ-2RKF1203X | Resistor, 120k, 0402 | Y | Digi-key | P120KLCT-ND
1 | R29 | P | Panasonic | ERJ-2GEJ105X | Resistor, 1M, 0402 | Y | Digi-key | P1.0MJTR-ND
4 | R32, R33, R34, R35 | P | Panasonic | ERJ-6GEY0R00V | Resistor, 0, 0805 | Y | Digi-key | P0.0ACT-ND
5 | R4, R7, R10, R13, R14 | P | Panasonic | ERJ-2GEJ103X | Resistor, 10k, 0402 | Y | Digi-key | ERJ-2GEJ103X
2 | R5, R6 | P | Panasonic | ERJ-2GEJ103X | Resistor, 4.7k, 0402 | Y | Digi-key | P10KJCT-ND
1 | R8 | P | Panasonic | ERJ-2RKF51R1X | Resistor, 51.1, 0402 | Y | Digi-key | P51.1LCT-ND
1 | R9 | P | Panasonic | ERJ-2RKF6191X | Resistor, 6.19k, 0402 | Y | Digi-key | P6.19KLCT-ND
1 | U1 | P | Atheros | AR9271-AL1A | Atheros WiFi WLAN IC | N | AliExpress | N/A
1 | U2 | P | Microchip | AT24C04CXHMT | EEPROM with I2C interface | N | Digi-key | AT24C04C-XHM-TCT-ND
4 | U3, U4, U5, U6 | P | Analog Devices | LT3080EQ#PBF | Adj. 1.1A Single Res LDO Regulator | N | Digi-key | LT3080EQ#PBF-ND
1 | Y1 | P | ECS International | ECS-400-10-36-CKY-TR | Crystal 40mhz 10pf Smd | N | Digi-key | XC2666CT-ND
VERSION INFO
Rev | Date | Notes
1 | 2019-09-17 | First rev BOM

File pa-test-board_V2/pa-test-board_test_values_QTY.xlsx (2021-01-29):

Qty | Refs | MFR | MPN | Value | DESCRIPTION
4 | C15, C16, C17, C18 | TDK | CGA2B1X7R1C104K050BC | 100nF | CAP CER 0.1UF 16V X7R 0402
1 | C19 | TDK | CGA2B2NP01H102J050BA | 1000pF | CAP CER 1000PF 50V NP0 0402
1 | C20 | Murata | GCM1885C1H101JA16D | 100pF | CAP CER 100PF 50V C0G/NP0 0603
1 | C21 | AVX | 04025U3R0BAT2A | 3.0pF | CAP CER 3PF 50V NP0 0402
1 | C22 | AVX | 04025J1R1PBSTR\500 | 1.1pF | 50V 1.1pF .02pFTol ThinFilm 0402
1 | C23 | AVX | 04025U1R6BAT2A | 1.6pF | CAP CER 1.6PF 50V NP0 0402
1 | C34 | Murata | GCJ31CR71C475KA01L | 4.7uF | CAP CER 4.7UF 16V X7R 1206
1 | C35 | Murata | GCJ32ER71C226KE01L | 22uF | CAP CER 22UF 16V X7R 1210
4 | J1, J2, J3, J4 | Cinch Connectivity Solutions Johnson | 142-0701-851 |  | CONN SMA JACK STR 50OHM EDGE MNT
1 | JP6 | Molex | 22232041 |  | CONN HEADER VERT 1x4POS 2.54MM
1 | L2 | Coilcraft | 1008HQ-10NXJLB | 10nH | Fixed Inductors 1008 10nH Unshld 5% 1.6A 60mOhms
1 | L3 | TDK Corporation | MLK1005S1N0ST000 | 1.0nH | FIXED IND 1NH 500MA 100 MOHM 0402 SMD
1 | L4 | Coilcraft | 0402DC-1N7XJRU | 1.7nH | 1.7nH RF Inductor, ceramic core, 5% tol, SMT, RoHS
1 | L5 | Coilcraft | 0805CS-060XJLC | 6.8n | Fixed Inductors 0805CS 6.8 nH 5 % 0.6 A
1 | LED1 | Lite-On | LTST-C193KRKT-5A |  | LED,SMD,0603,Red,Lite-On 1608 (0603), Rectangle Lens SMD Package
1 | LED2 | Lite-On | LTST-C193KGKT-5A |  | LED,SMD,0603,Green,Lite-On 1608 (0603), Rectangle Lens SMD Package
1 | R1 | Panasonic Electronic Components | ERJ-2GE0R00X | 0 | RES SMD 0 OHM JUMPER 1/10W 0402
1 | R17 | Panasonic | ERJ-6GEY0R00V | 0 | RES SMD 0 OHM JUMPER 1/8W 0805
1 | R19 | Panasonic | ERJ-2RKF1100X | 110 | RES SMD 110 OHM 1% 1/10W 0402
1 | R20 | Panasonic | ERJ-3EKF2200V | 220 | RES SMD 220 OHM 1% 1/10W 0603
2 | R32, R36 | Panasonic | ERJ-2GEJ102X | 1k | RES SMD 1K OHM 5% 1/10W 0402
1 | SW1 | APEM Inc. | TL36P005000 |  | SWITCH TOGGLE SPDT 0.4VA 20V
1 | U10 | Qorvo | TQP9111 |  | RF Amplifier 1.8-2.7GHz Gn 29.8dB P1dB 32.5dBm 2 stage

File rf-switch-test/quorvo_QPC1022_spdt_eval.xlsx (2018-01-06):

Bill Of Materials for Qorvo QPC1022 SPDT RF Switch Board
source file: quorvo_QPC1022_spdt_eval.sch
Last modified: 2018/01/05
PCB version: 1 |  |  | P/DNP = | Place/Do Not Place (DNP is for final production boards)
BOM revision: 0 |  |  | Generic = | Any generic part with the same characteristics are OK (e.g., bypass cap)
Cnt | Part References | P/DNP | Mfg | Mfg PN | Description | Distributor | Dist. PN | Generic | Notes
3 | CF1,CF2,CF3 | P | Cinch | 142-0701-806 | SMA Connector Jack, Female Socket 50 Ohm Board Edge | Digi-Key | J716-ND | Y
1 | U1 | P | Qorvo | QPC1022 | RF Switch ICs 5-6000MHz SPDT IL .25dB Iso 39dB | Mouser | 772-QPC1022SR | N
1 | R1 | P |  |  | 10k ohm 0603 1% resistor |  |  | Y
1 | R2 | P |  |  | 5.63k ohm 0603 1% resistor |  |  | Y
1 | C1 | P |  |  | 100n 0402 X7R > 10V capacitor |  |  | Y
2 | C2,C3 | P |  |  | 100p 0402 X7R > 10V capacitor |  |  | Y
1 | C4 | P |  |  | 10u 0805 X7R > 10V capacitor |  |  | Y

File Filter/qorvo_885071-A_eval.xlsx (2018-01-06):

Bill Of Materials for Qorvo 885071-A Band Pass Filter Evaluation Board
source file: qorvo_885071-A_eval.sch
Last modified: 2018/01/05
PCB version: 1 |  |  | P/DNP = | Place/Do Not Place (DNP is for final production boards)
BOM revision: 0 |  |  | Generic = | Any generic part with the same characteristics are OK (e.g., bypass cap)
Cnt | Part References | P/DNP | Mfg | Mfg PN | Description | Distributor | Dist. PN | Generic | Notes
4 | CF1,CF2,CF3,CF4 | P | Cinch | 142-0701-806 | SMA Connector Jack, Female Socket 50 Ohm Board Edge | Digi-Key | J716-ND | Y
1 | U1 | P | Qorvo | 885071-A | Signal Conditioning 2.4GHz -40C +95C BAW | Mouser | 772-885071-A | N
1 | L1 | P |  |  | 7.5 nH 0402 inductor with f>2.4 ghz |  |  | Y
1 | L2 | P |  |  | 8.2 nH 0402 inductor with f > 2.4 Ghz |  |  | Y

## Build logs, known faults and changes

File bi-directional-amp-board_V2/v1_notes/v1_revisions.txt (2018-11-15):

U6 footprint:
	need to change mask and cream layer to only cover actual pad
R6 silk
diode silk
R39 looks like R3
r31 close to l10
c21,22,23, 26 28 footprint wrong
c7 c8 swaped
c30 c31 swapped
u8 looks like j8
double check each IC has silk outline
l1 pad is too large

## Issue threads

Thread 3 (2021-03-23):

Missing RF tStop

NickLekas, 2021-03-23:
The tStop mask is missing along the RF trace.

NickLekas, 2021-04-05:
Fixed

Closed 2021-04-05.

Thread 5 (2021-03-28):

Switch JP107 footprint so it has a fixed pullup

NickLekas, 2021-03-28:

NickLekas, 2021-04-05:
Fixed

Closed 2021-04-05.

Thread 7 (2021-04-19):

All power for the WF should come from the Octavo

NickLekas, 2021-04-19:
WIFI_ENABLE and WIFI_STATUS should source power from USB_HO_VBUS instead of 5V

andrewgreenberg, 2021-04-19:
Make R21 and R29 to be 4.7k

NickLekas, 2021-04-19:
Fixed

Closed 2021-04-19.

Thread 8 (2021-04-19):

Add zero ohm resistors on the outputs of all switching power supplies.

andrewgreenberg, 2021-04-19:
If it's easy-ish, breakout the Enable pin from the SPS and pull it up with a 10k and put a test point on it, so we can disable that power supply.

Closed 2022-05-04.

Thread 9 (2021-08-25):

Placeholder: Connect USB1_VBUS to USB VDD in such a way that the USB hub enumerates correctly

oliver-rew, 2021-08-25:
We aren't sure exactly what needs to happen yet, but this ticket is a place holder for it and another board rev should not happen until fixed

davidalay, 2022-05-03:
resolved on V1.2 with the new TUSB4020 chip

Closed 2022-05-03.

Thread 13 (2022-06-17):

Change reference path of the title block to work with the kicad plugin.  Correct title block is in the oresat-kicad repo.

davidalay, 2022-06-17:

andrewgreenberg, 2022-11-07:
Not sure if still relevant.

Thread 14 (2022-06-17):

Change attributes to reflect the BOM changes.

davidalay, 2022-06-17:
The BOM spreadsheet pushed in commit 7567d3d00f25bbc5323c2c029a8bf12caa3b2095 is correct, attributes should be back populated based off this

andrewgreenberg, 2022-11-07:
Not sure if still relevant.

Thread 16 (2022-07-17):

Connect OPD UART to UART0

cesarordaz, 2022-07-17:
UART lines from the TS5A21366 OPD UART switch should be connected to UART0 which goes to the debug connector.
This is so that the C3 can communicate directly with the Octavo.

i.e. the nets UART0_Tx(C3-Rx) and UART0_Rx(C3-Tx) should be changed to UART0_Tx and UART0_Rx.

NickLekas, 2022-11-07:
Done

Closed 2022-11-07.

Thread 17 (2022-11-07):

Fix ground on layers 2 and 3 under 5V SPS ICs

andrewgreenberg, 2022-11-07:

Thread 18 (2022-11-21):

Fix boot jumper placement

NickLekas, 2022-11-21:
rearrange boot jumpers JP105-109 to match the order referenced in printed boot instructions

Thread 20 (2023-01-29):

SD card slot frame interferance

NickLekas, 2023-01-29:
Move the SD card slot further into the card. An SD card cannot be in the slot while enclosed in the satellite

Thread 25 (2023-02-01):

Fix broken 1.1V schematic symbol

NickLekas, 2023-02-01:

NickLekas, 2023-02-20:
fixed

Closed 2023-02-20.

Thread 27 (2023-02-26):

Solder stop on SMPM missing

NickLekas, 2023-02-26:

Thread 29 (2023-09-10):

Connect 5V to USB1_VBUS

cesarordaz, 2023-09-10:
The Octavo expects to see 5V on the USB1_VBUS pin after it determines that the port is in host mode. The _right_ way to do this would be a switch controlled by USB1_DRVVBUS connecting 5V to USB1_VBUS, but we did find that it also works if you directly connect 5V to the pin.
One of these fixes should be implemented so that the USB hub will work.

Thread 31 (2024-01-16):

Q5 and Q6 are backward

andrewgreenberg, 2024-01-16:
Q5 and Q6 are backwards; the body diode points forward. Start v1.4 and fix, and also fix both other boards.

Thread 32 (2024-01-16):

Remove D14 from OPD

andrewgreenberg, 2024-01-16:
D14 bootstraps the OPD, so it stays on through a C3 reset. This is extremely bad :/

* Remove D14 from existing DXWiFi cards
* Remove D14 from CAD in >= v1.4.

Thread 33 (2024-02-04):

Wrong netclass on several RF nets

ojones808, 2024-02-04:
Several of the nets in the RF path are "default" rather than "RF", resulting in ground being to close to the RF trace.

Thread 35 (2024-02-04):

Attenuator between RF input and matching network causes matching issue

ojones808, 2024-02-04:
The pi-pad attenuator upsets the match, reducing S11 and S21. Need to either replace with a commercial SMT part such as Ohmite TFA series, or  rework existing pi-pad be replacing R88 and R87 with a single 294 Ohm resistor, possibly going to 0402 for all of the resistors, and improving the grounding with more ground vias close to the resistors. Suggest we make test boards to evaluate these approaches.

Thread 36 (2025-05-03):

PA sheet missing component values

NickLekas, 2025-05-03:
Most passives on the PA sheet do not have component values. A MPN is assigned to them but no value is entered in KiCAD.

NickLekas, 2025-05-03:
All resistor arrays have the same issue

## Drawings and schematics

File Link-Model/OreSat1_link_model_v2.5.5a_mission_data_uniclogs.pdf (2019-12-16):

OreSat1 - Bulk Mission Uplink / Telecommand | OreSat1 - Bulk Mission Downlink / Telemetry

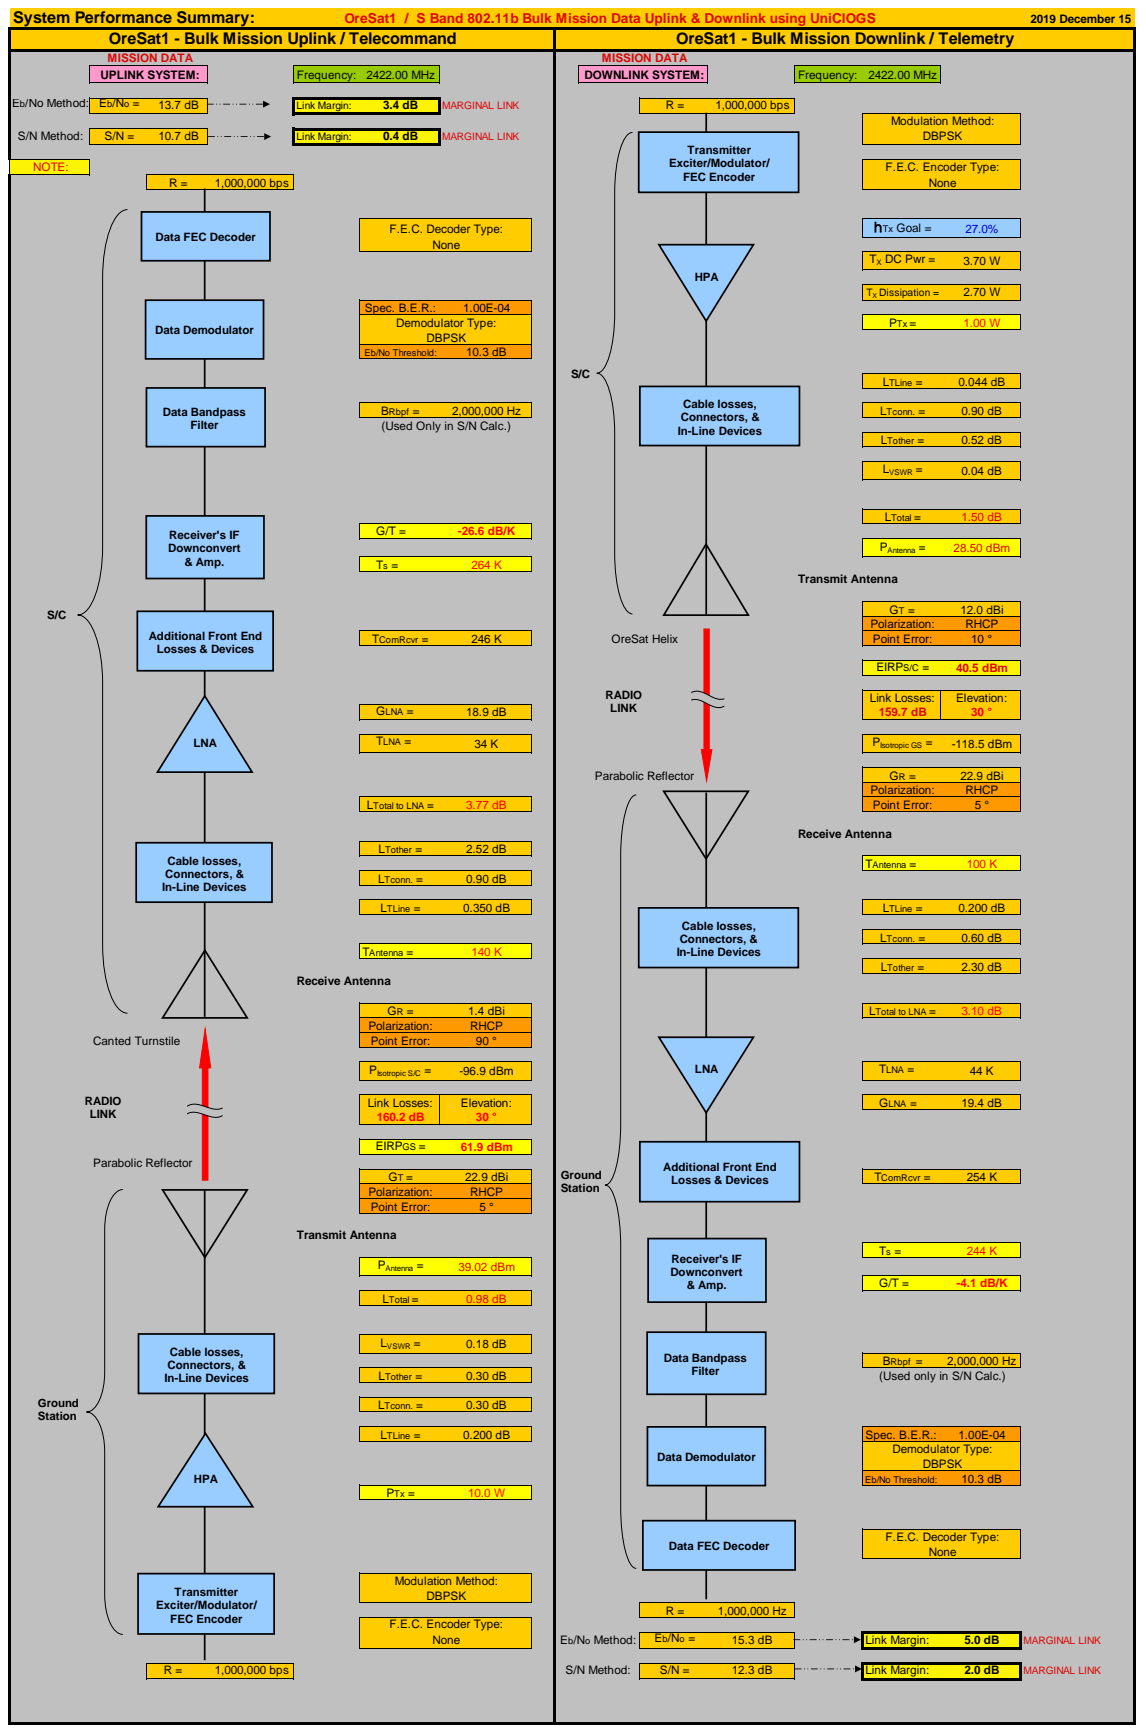
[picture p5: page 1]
System Performance Summary:; OreSat1 / S Band 802.11b Bulk Mission Data Uplink & Downlink using UniClOGS; 2019 December 15; Frequency: 2422.00 MHz; Eb/No Method:; Link Margin:; MARGINAL LINK; 1,000,000 bps; S/N Method:; NOTE:; hTx Goal =; TX DC Pwr =; TX Dissipation =; Spec. B.E.R.:; PTx =; Eb/No Threshold:; LTLine =; BRbpf =; LTconn. =; LTother =; LVSWR =; LTotal =; PAntenna =; 28.50 dBm; Transmit Antenna; 12.0 dBi; Polarization:; RHCP; TComRcvr =; Point Error:; EIRPS/C =; 40.5 dBm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

MISSION DATA | MISSION DATA

Data FEC Decoder

(Used Only in S/N Calc.)

Cable losses,
Connectors, &
In-Line Devices

Additional Front End
Losses & Devices

(Used only in S/N Calc.)

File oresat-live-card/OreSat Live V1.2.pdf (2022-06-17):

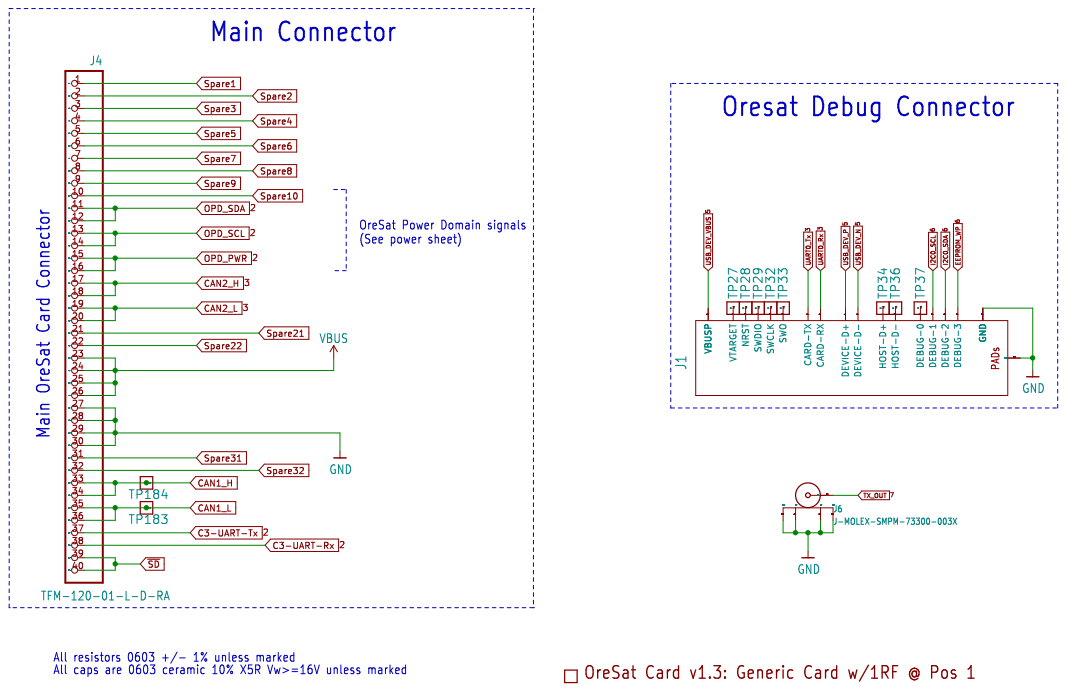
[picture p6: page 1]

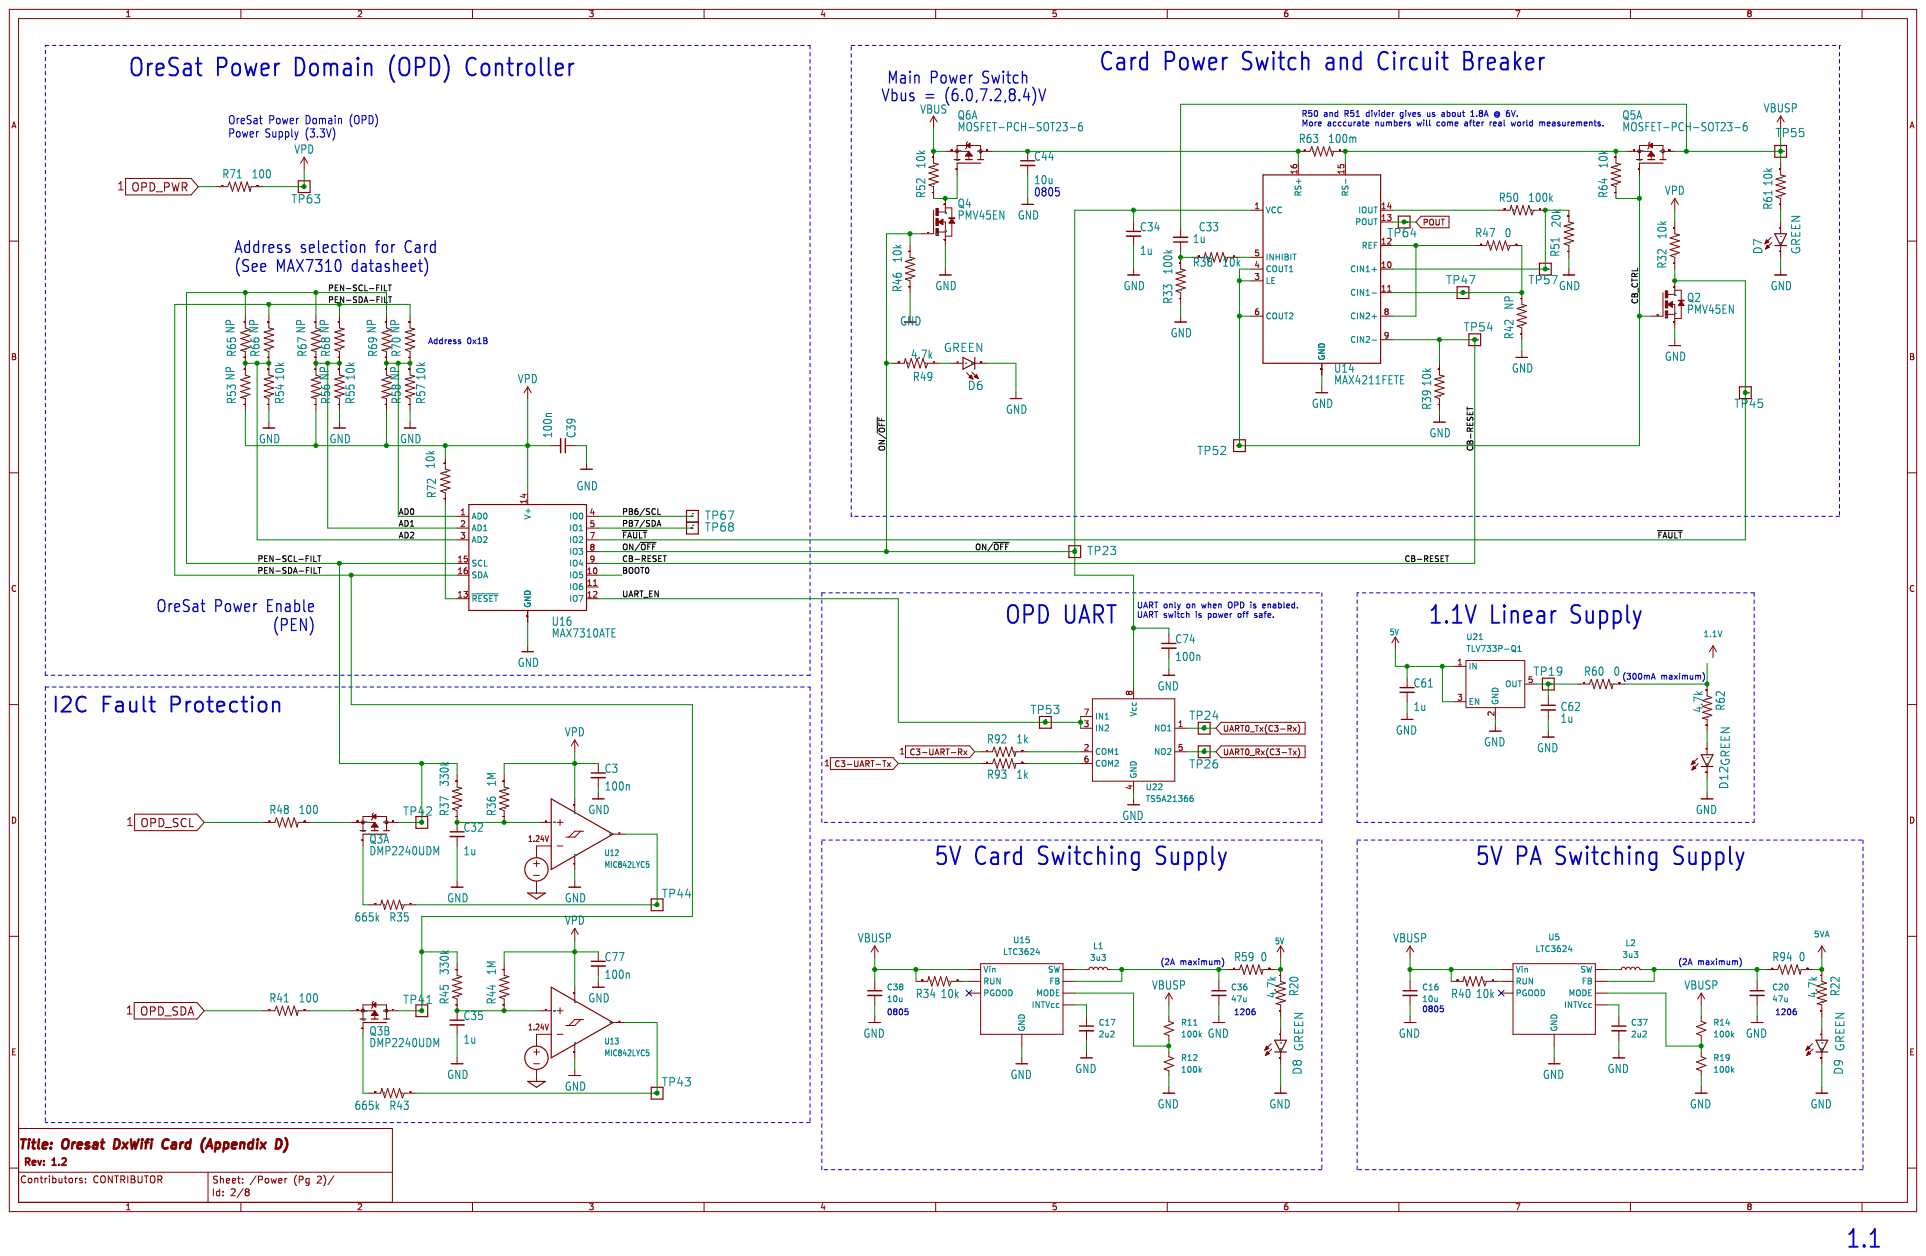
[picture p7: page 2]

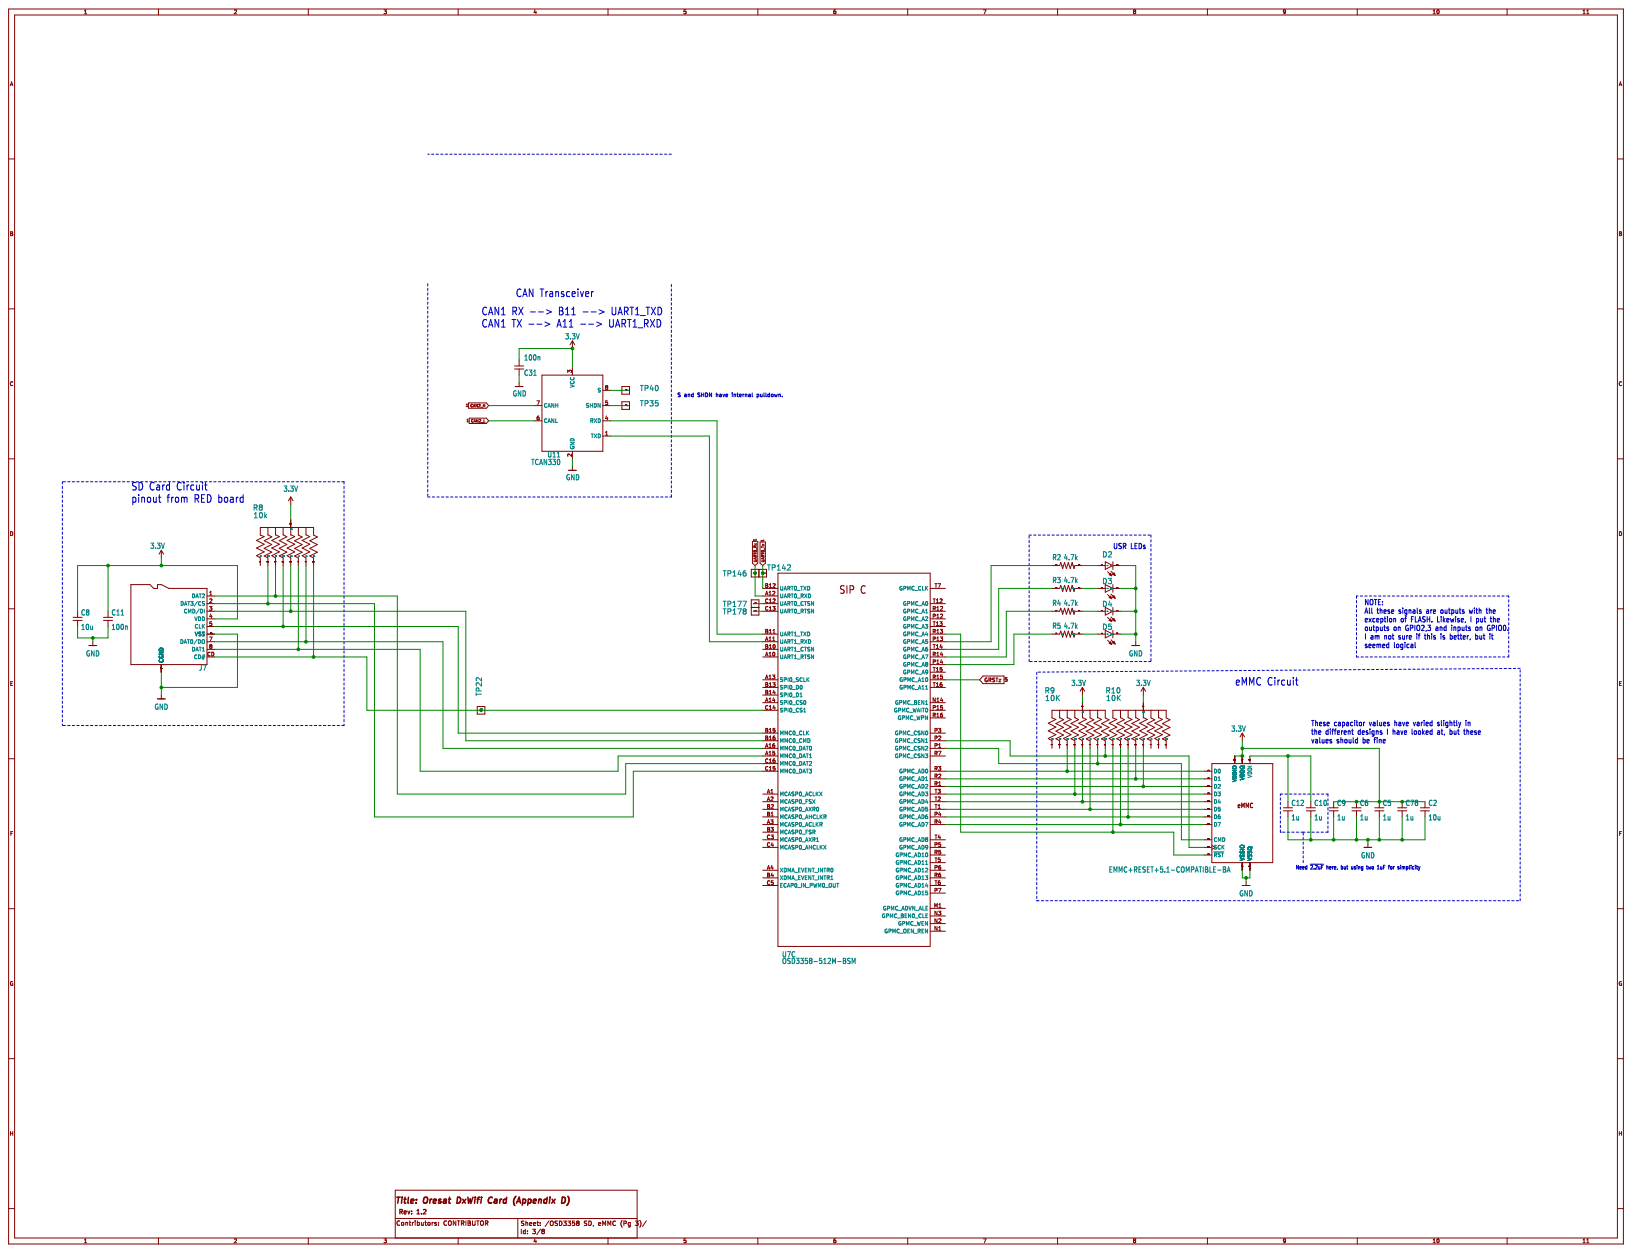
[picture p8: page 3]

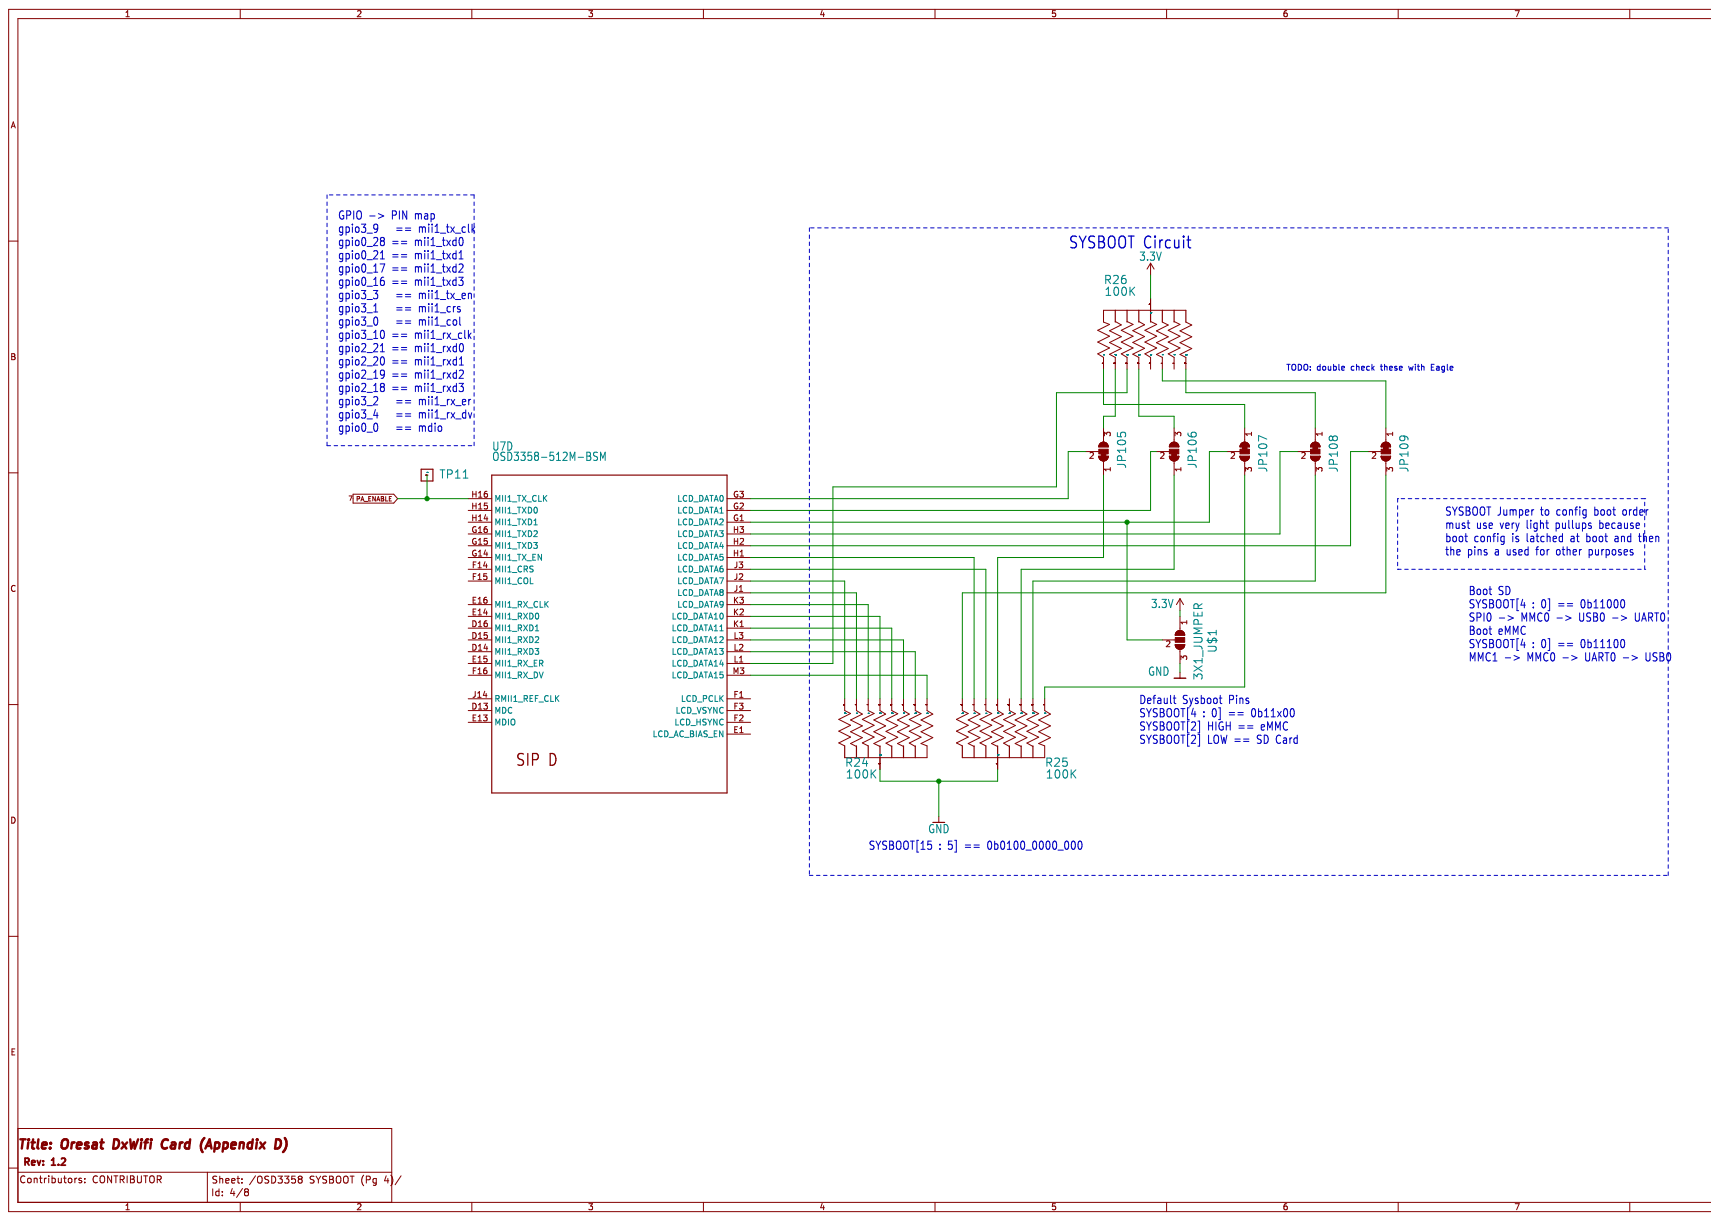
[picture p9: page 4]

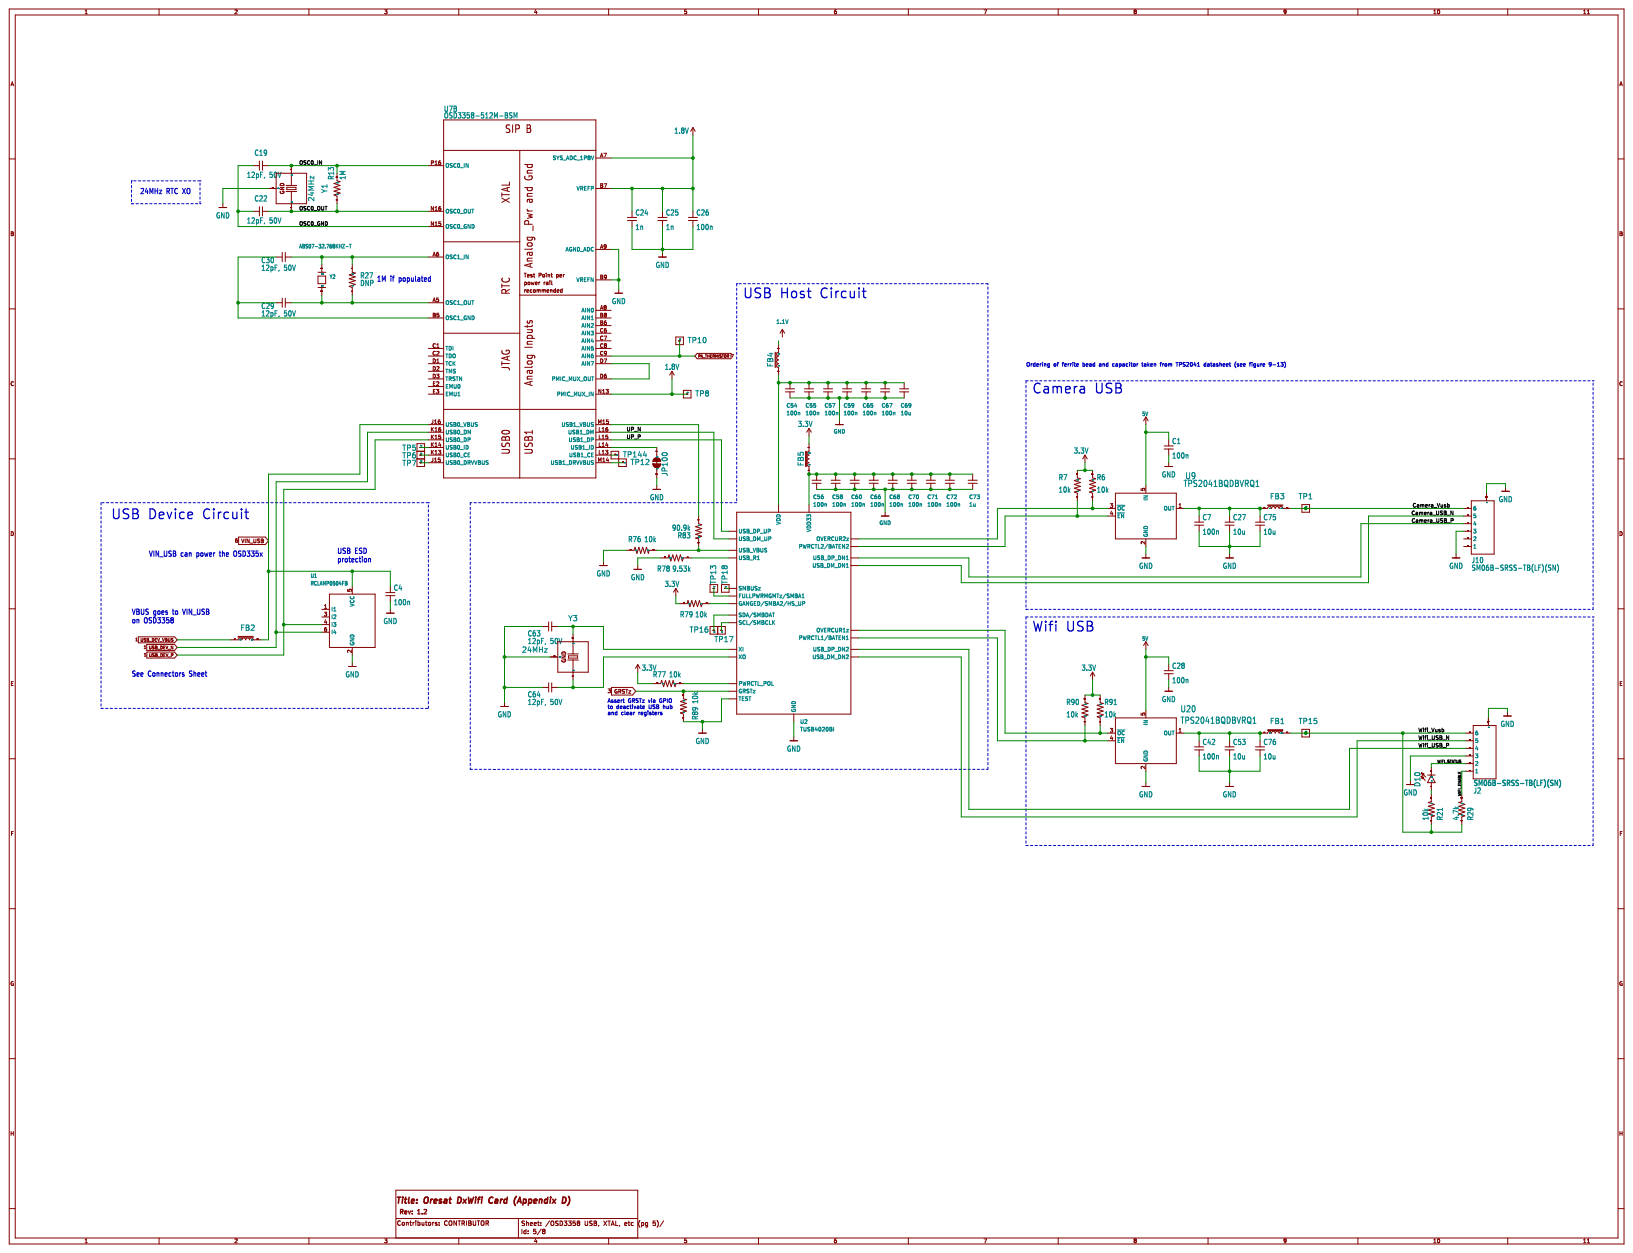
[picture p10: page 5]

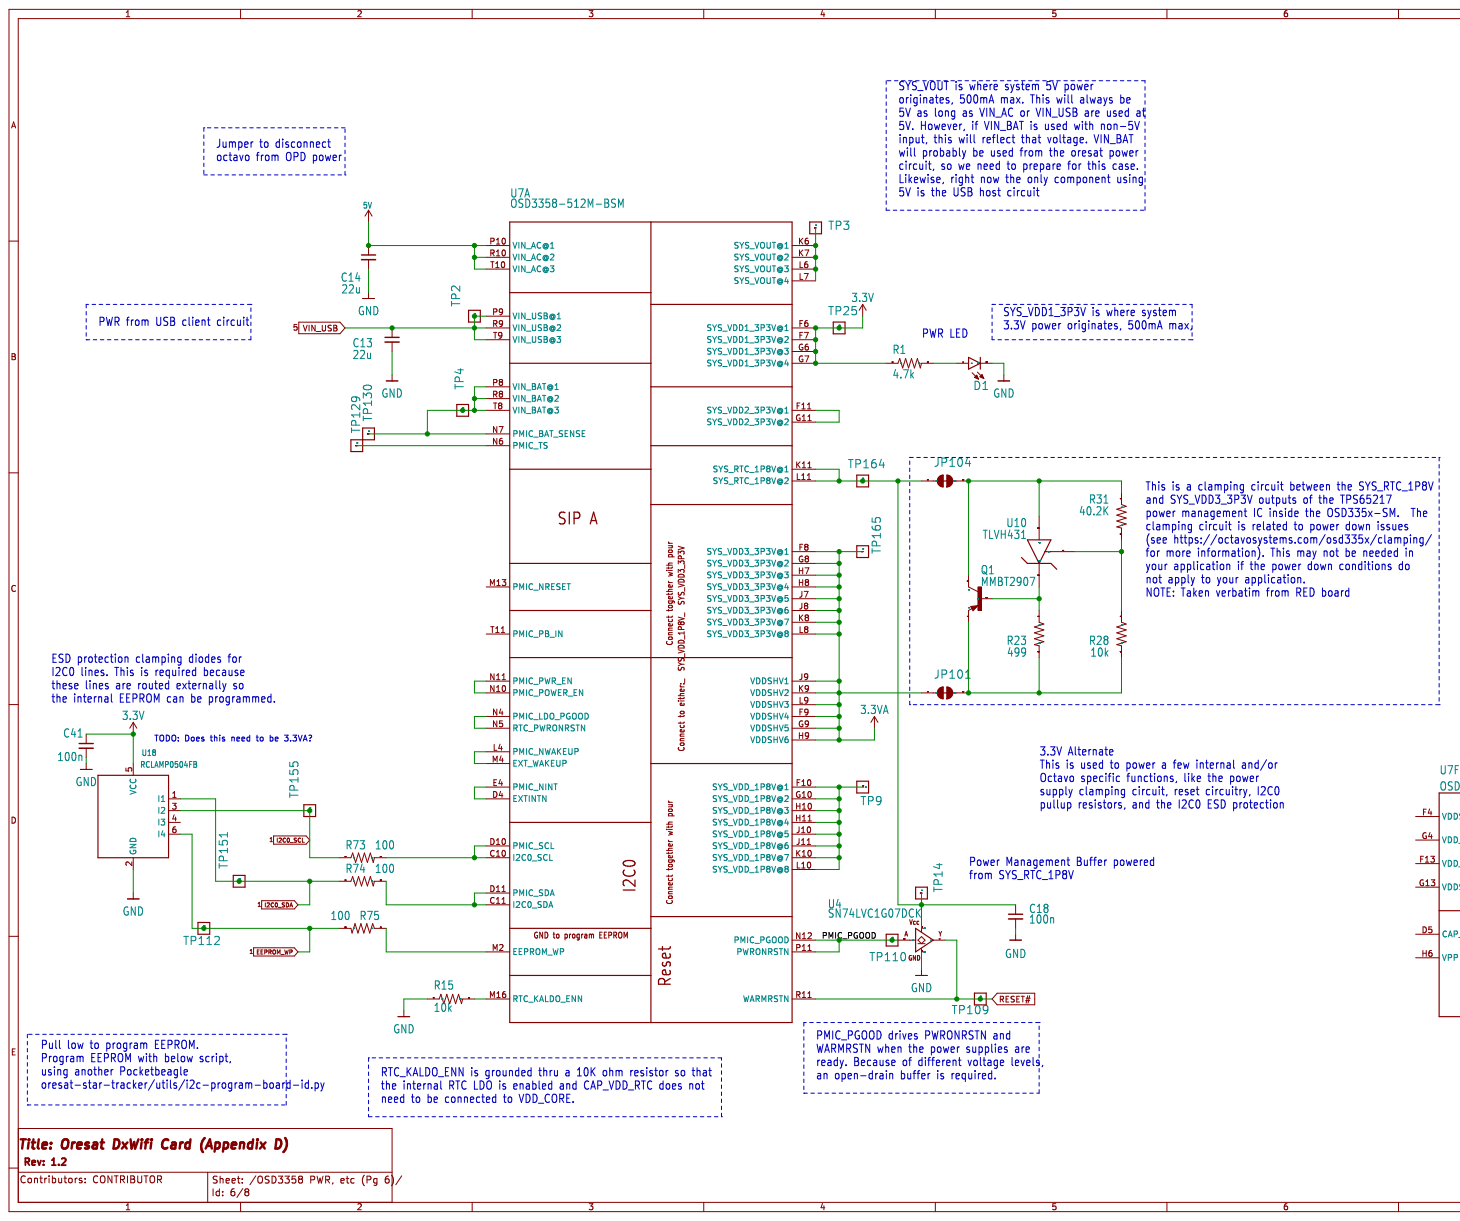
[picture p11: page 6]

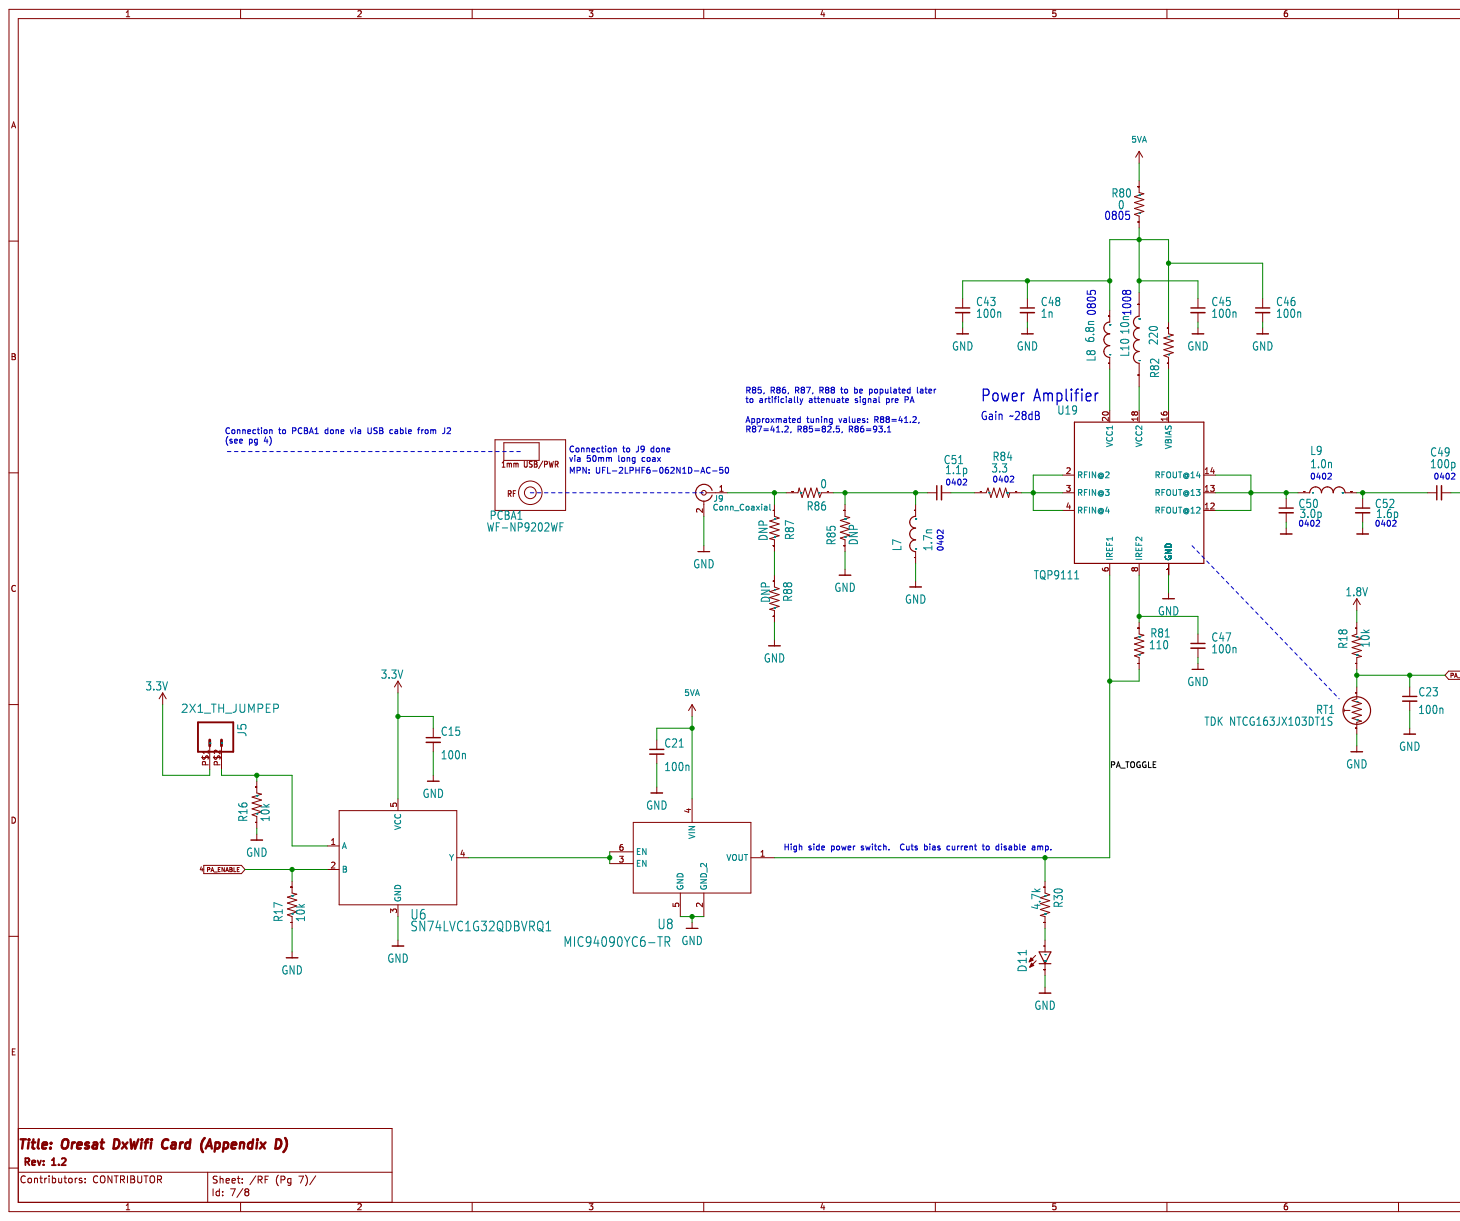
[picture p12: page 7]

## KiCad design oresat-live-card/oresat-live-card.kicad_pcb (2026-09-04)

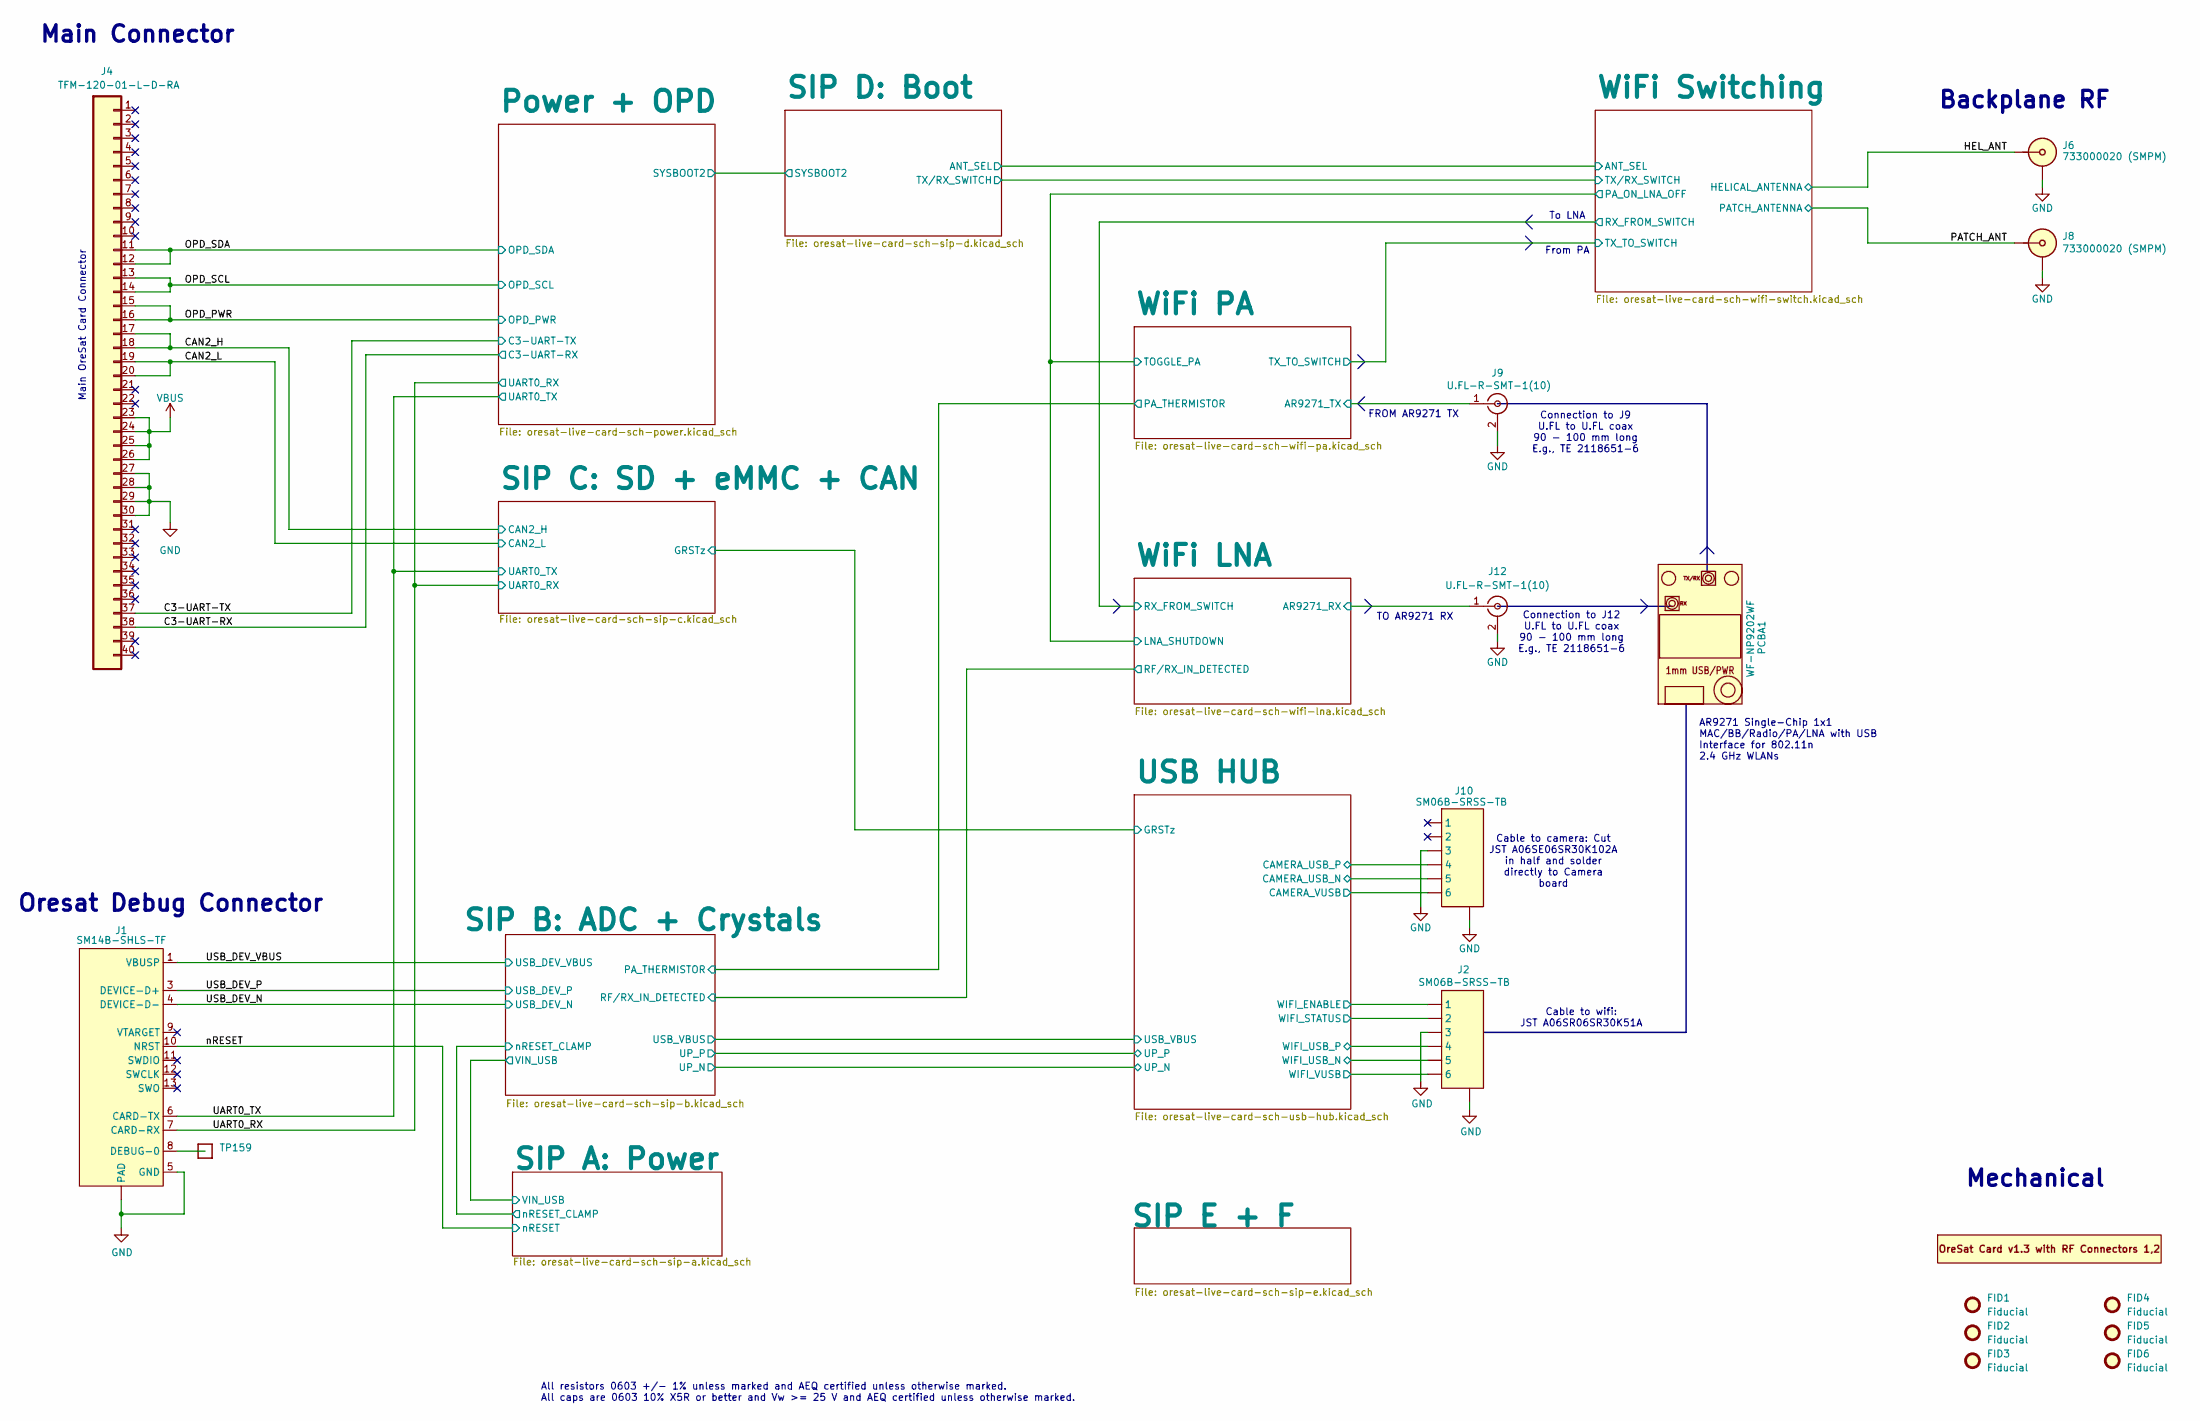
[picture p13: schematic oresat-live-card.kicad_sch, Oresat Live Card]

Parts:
FID1, FID2, FID3, FID4, FID5, FID6: Fiducial; Fiducial_1mm_Mask2mm
J1: SM14B-SHLS-TF; J-JST-SM14BSHLSTF; MPN SM14B-SHLS-TF
J2, J10: SM06B-SRSS-TB; CONN_SM06B-SRSS-TB_JST; MPN SM06B-SRSS-TB
J4: TFM-120-01-L-D-RA; J-SAMTEC-TFM-120-X1-XXX-D-RA; MPN TFM-120-01-L-D-RA
J6, J8: 733000020 (SMPM); J-MOLEX-SMPM-073300-002X; MPN 733000020
J9, J12: U.FL-R-SMT-1(10); U.FL_Molex_MCRF_73412-0110_Vertical; MPN U.FL-R-SMT-1(10)
PCB1: ORESAT-CARD-V1.3-GENERIC-1RF-POS1; ORESAT-CARD-V1.3-2RF-LEFT; MPN N/A
PCBA1: WF-NP9202WF; WF-NP9202; MPN WF-NP9202WF
TP159: 0.03x0.04; TestPoint-0.75mm-th

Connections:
/C3-UART-RX: J4.38; also elsewhere on the board
/C3-UART-TX: J4.37; also elsewhere on the board
/CAN2_H: J4.17, J4.18; also elsewhere on the board
/CAN2_L: J4.19, J4.20; also elsewhere on the board
/HEL_ANT: J6.1 (SIG); also elsewhere on the board
/OPD_PWR: J4.15, J4.16; also elsewhere on the board
/OPD_SCL: J4.13, J4.14; also elsewhere on the board
/OPD_SDA: J4.11, J4.12; also elsewhere on the board
/PATCH_ANT: J8.1 (SIG); also elsewhere on the board
/UART0_RX: J1.7 (CARD-RX); also elsewhere on the board
/UART0_TX: J1.6 (CARD-TX); also elsewhere on the board
/USB HUB/CAMERA_USB_N: J10.5; also elsewhere on the board
/USB HUB/CAMERA_USB_P: J10.4; also elsewhere on the board
/USB HUB/CAMERA_VUSB: J10.6; also elsewhere on the board
/USB HUB/WIFI_ENABLE: J2.1; also elsewhere on the board
/USB HUB/WIFI_STATUS: J2.2; also elsewhere on the board
/USB HUB/WIFI_USB_N: J2.5; also elsewhere on the board
/USB HUB/WIFI_USB_P: J2.4; also elsewhere on the board
/USB HUB/WIFI_VUSB: J2.6; also elsewhere on the board
/USB_DEV_N: J1.4 (DEVICE-D-); also elsewhere on the board
/USB_DEV_P: J1.3 (DEVICE-D+); also elsewhere on the board
/USB_DEV_VBUS: J1.1 (VBUSP), J1.2 (VBUSP); also elsewhere on the board
/WiFi LNA/AR9271_RX: J12.1 (In); also elsewhere on the board
/WiFi PA/AR9271_TX: J9.1 (In); also elsewhere on the board
/nRESET: J1.10 (NRST); also elsewhere on the board
GND: J1.5 (GND), J1.14 (GND), J1.15 (PAD), J1.16 (PAD), J2.3, J2.7, J2.8 (7), J4.27, J4.28, J4.29, J4.30, J6.2 (SHLD), J8.2 (SHLD), J9.2 (Ext), J10.3, J10.7, J10.8 (7), J12.2 (Ext); also elsewhere on the board
unnamed: J1.8 (DEBUG-0), TP159.1 (1_1)
VBUS: J4.23, J4.24, J4.25, J4.26; also elsewhere on the board

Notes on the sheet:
Mechanical
All resistors 0603 +/- 1% unless marked and AEQ certified unless otherwise marked. All caps are 0603 10% X5R or better and Vw >= 25 V and AEQ certified unless otherwise marked.
TO AR9271 RX
Main Connector
Main OreSat Card Connector
FROM AR9271 TX
From PA
Connection to J12 U.FL to U.FL coax 90 - 100 mm long E.g., TE 2118651-6
Connection to J9 U.FL to U.FL coax 90 - 100 mm long E.g., TE 2118651-6
AR9271 Single-Chip 1x1 MAC/BB/Radio/PA/LNA with USB Interface for 802.11n 2.4 GHz WLANs
To LNA
Cable to wifi: JST A06SR06SR30K51A
Cable to camera: Cut JST A06SE06SR30K102A in half and solder directly to Camera board
Oresat Debug Connector
Backplane RF

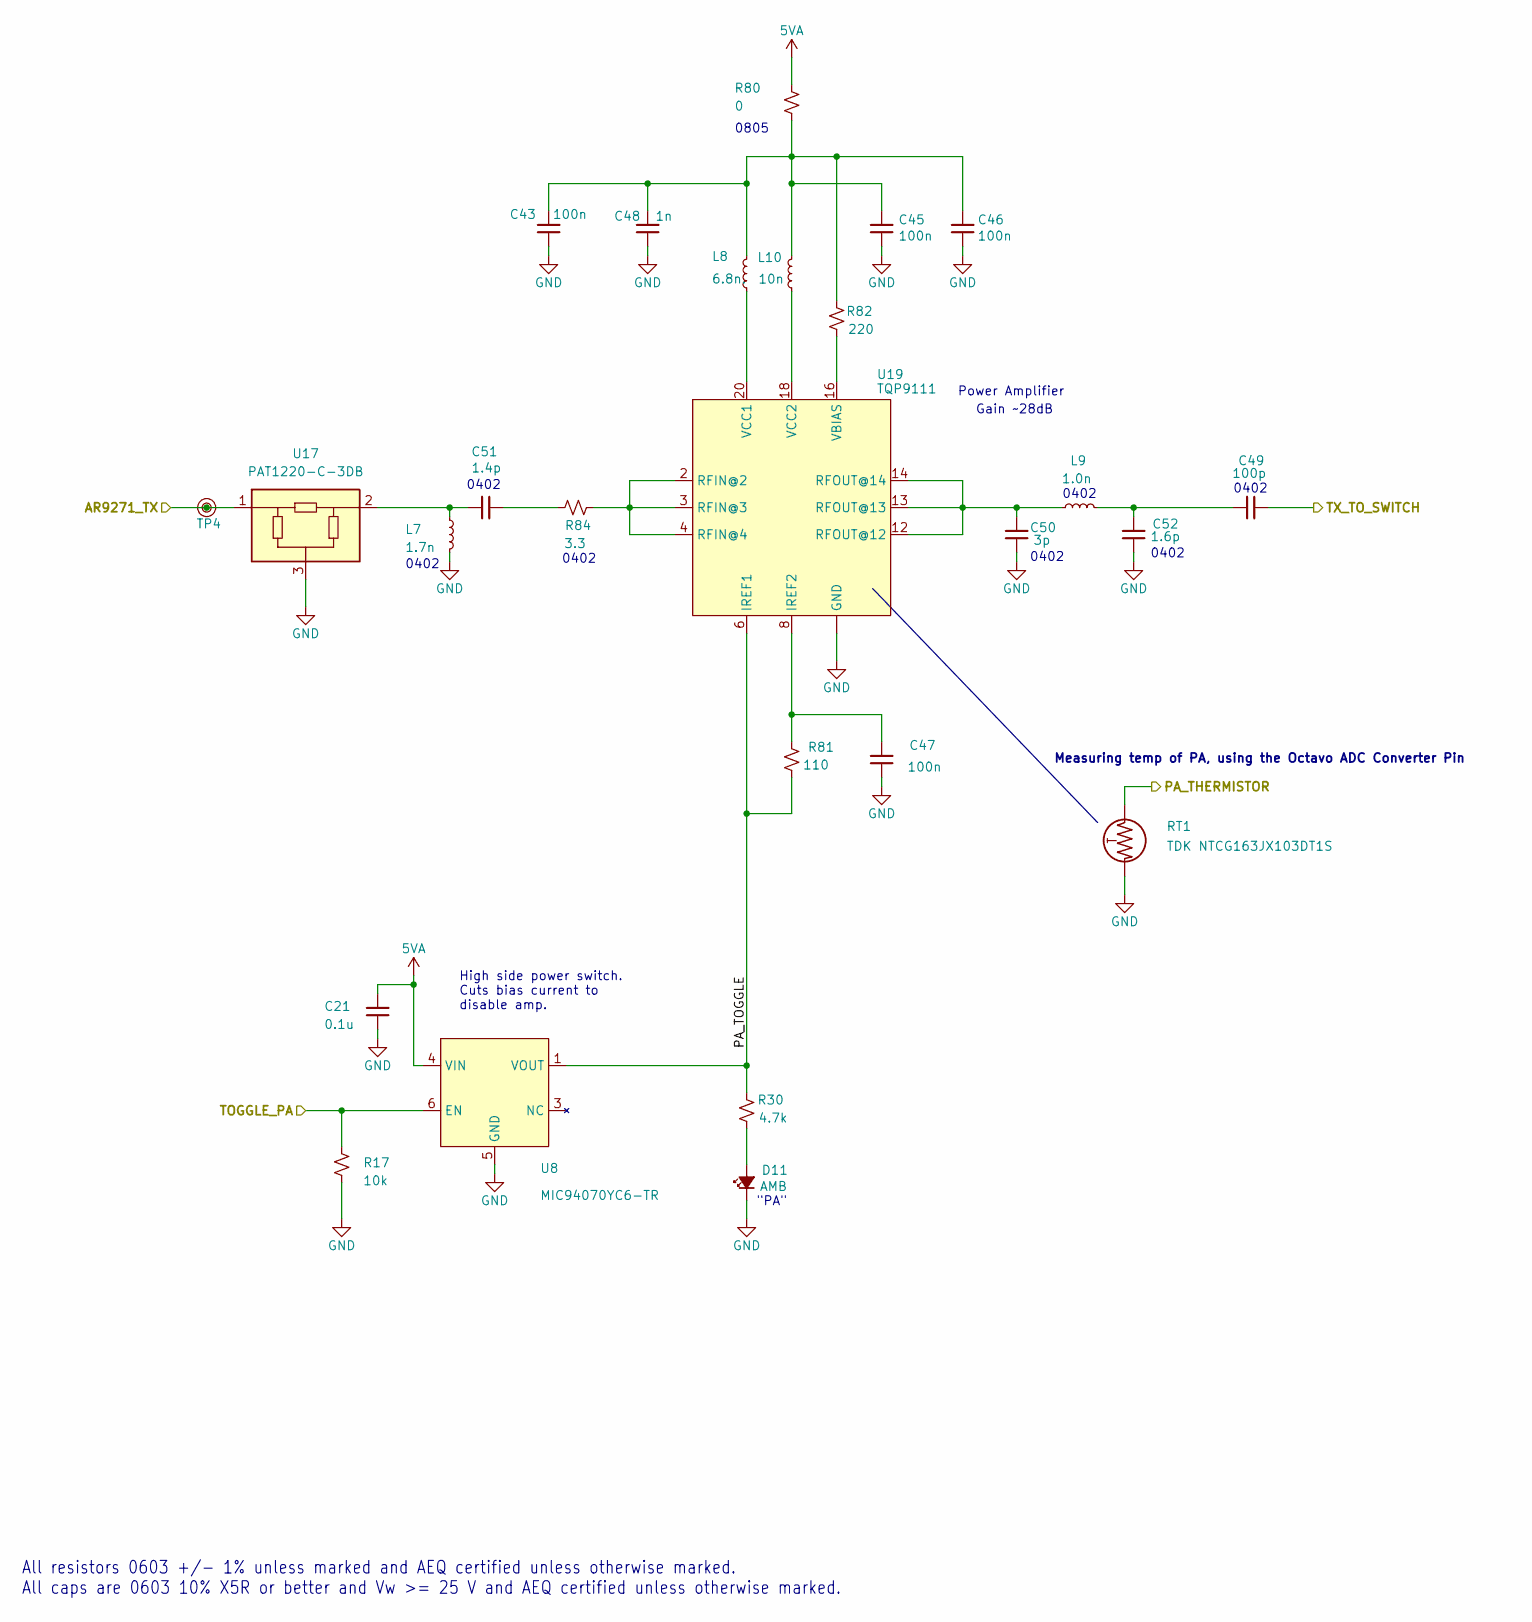
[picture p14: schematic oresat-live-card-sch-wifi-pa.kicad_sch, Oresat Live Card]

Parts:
C21: 0.1u; 0603-C-NOSILK; MPN C0603C104K5RACAUTO
C43, C45, C46, C47: 100n; 0603-C-NOSILK; MPN CGA3E2X7R1E104K080AA
C48: 1n; 0402-C-NOSILK; MPN CGA2B2NP01H102J050BA
C49: 100p; 0402-C-NOSILK; MPN GCM1555C1H101GA16D
C50: 3p; 0402-C-NOSILK; MPN 04025U3R0BAT2A
C51: 1.4p; 0402-C-NOSILK; MPN 04025J1R1PBSTR\500
C52: 1.6p; 0402-C-NOSILK; MPN 04025U1R6BAT2A
D11: AMB; LED-0603; MPN 150060AS75000
L7: 1.7n; 0402-C-NOSILK; MPN 0402DC-1N7XJRW
L8: 6.8n.; 0805-C-NOSILK; MPN 0805CS-060XJRC
L9: 1.0n; 0402-C-NOSILK; MPN MLK1005S1N0ST000
L10: 10n; INDC2928X203N; MPN 1008HQ-10NXJLC
R17: 10k; 0603-C-NOSILK; MPN RMCF0603FT10K0
R30: 4.7k; 0603-C-NOSILK; MPN RMCF0603FT4K70
R80: 0; 0805-C-NOSILK; MPN ERJ-6GEY0R00V
R81: 110; 0402-C-NOSILK; MPN ERJ-2RKF1100X
R82: 220; 0603-C-NOSILK; MPN ERJ-3EKF2200V
R84: 3.3; 0402-C-NOSILK; MPN CRCW04023R30FKED
RT1: TDK NTCG163JX103DT1S; 0603-THERMISTOR-B; MPN NTCG163JX103DT1S
TP4: TestPoint_RF_Probe
U8: MIC94070YC6-TR; SC-70-6_MCH; MPN MIC94070YC6-TR
U17: PAT1220-C-3DB; RF_Attenuator_Susumu_PAT1220; MPN PAT1220-C-3DB-T5
U19: TQP9111; QFN50P400X400X102-21N; MPN TQP9111

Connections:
5VA: C21.1, R80.2, U8.4 (VIN); also elsewhere on the board
/SIP B: ADC + Crystals/PA_THERMISTOR: RT1.1; also elsewhere on the board
/WiFi LNA/LNA_SHUTDOWN: R17.2, U8.6 (EN); also elsewhere on the board
/WiFi PA/AR9271_TX: TP4.1 (1_1), U17.1; also elsewhere on the board
/WiFi PA/PA_TOGGLE: R30.1, R81.1, U8.1 (VOUT), U19.6 (IREF1)
/WiFi PA/TX_TO_SWITCH: C49.2; also elsewhere on the board
GND: C21.2, C43.2, C45.2, C46.2, C47.2, C48.2, C50.2, C52.2, D11.1 (K), L7.1, R17.1, RT1.2, U8.2 (GND), U8.5 (GND), U17.3, U19.1 (GND), U19.5 (GND), U19.7 (GND), U19.9 (GND), U19.10 (GND), U19.11 (GND), U19.15 (GND), U19.17 (GND), U19.19 (GND), U19.21 (GND); also elsewhere on the board
unnamed: C43.1, C45.1, C46.1, C48.1, L8.2, L10.2, R80.1, R82.2
unnamed: C49.1, C52.1, L9.2
unnamed: C51.1, L7.2, U17.2
unnamed: C51.2, R84.1
unnamed: D11.2 (A), R30.2
unnamed: C47.1, R81.2, U19.8 (IREF2)
unnamed: R84.2, U19.2 (RFIN@2), U19.3 (RFIN@3), U19.4 (RFIN@4)
unnamed: C50.1, L9.1, U19.12 (RFOUT@12), U19.13 (RFOUT@13), U19.14 (RFOUT@14)
unnamed: R82.1, U19.16 (VBIAS)
unnamed: L8.1, U19.20 (VCC1)
unnamed: L10.1, U19.18 (VCC2)

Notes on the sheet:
0402
"PA"
High side power switch. Cuts bias current to disable amp.
Gain ~28dB
0805
Measuring temp of PA, using the Octavo ADC Converter Pin
Power Amplifier
All resistors 0603 +/- 1% unless marked and AEQ certified unless otherwise marked. All caps are 0603 10% X5R or better and Vw >= 25 V and AEQ certified unless otherwise marked.

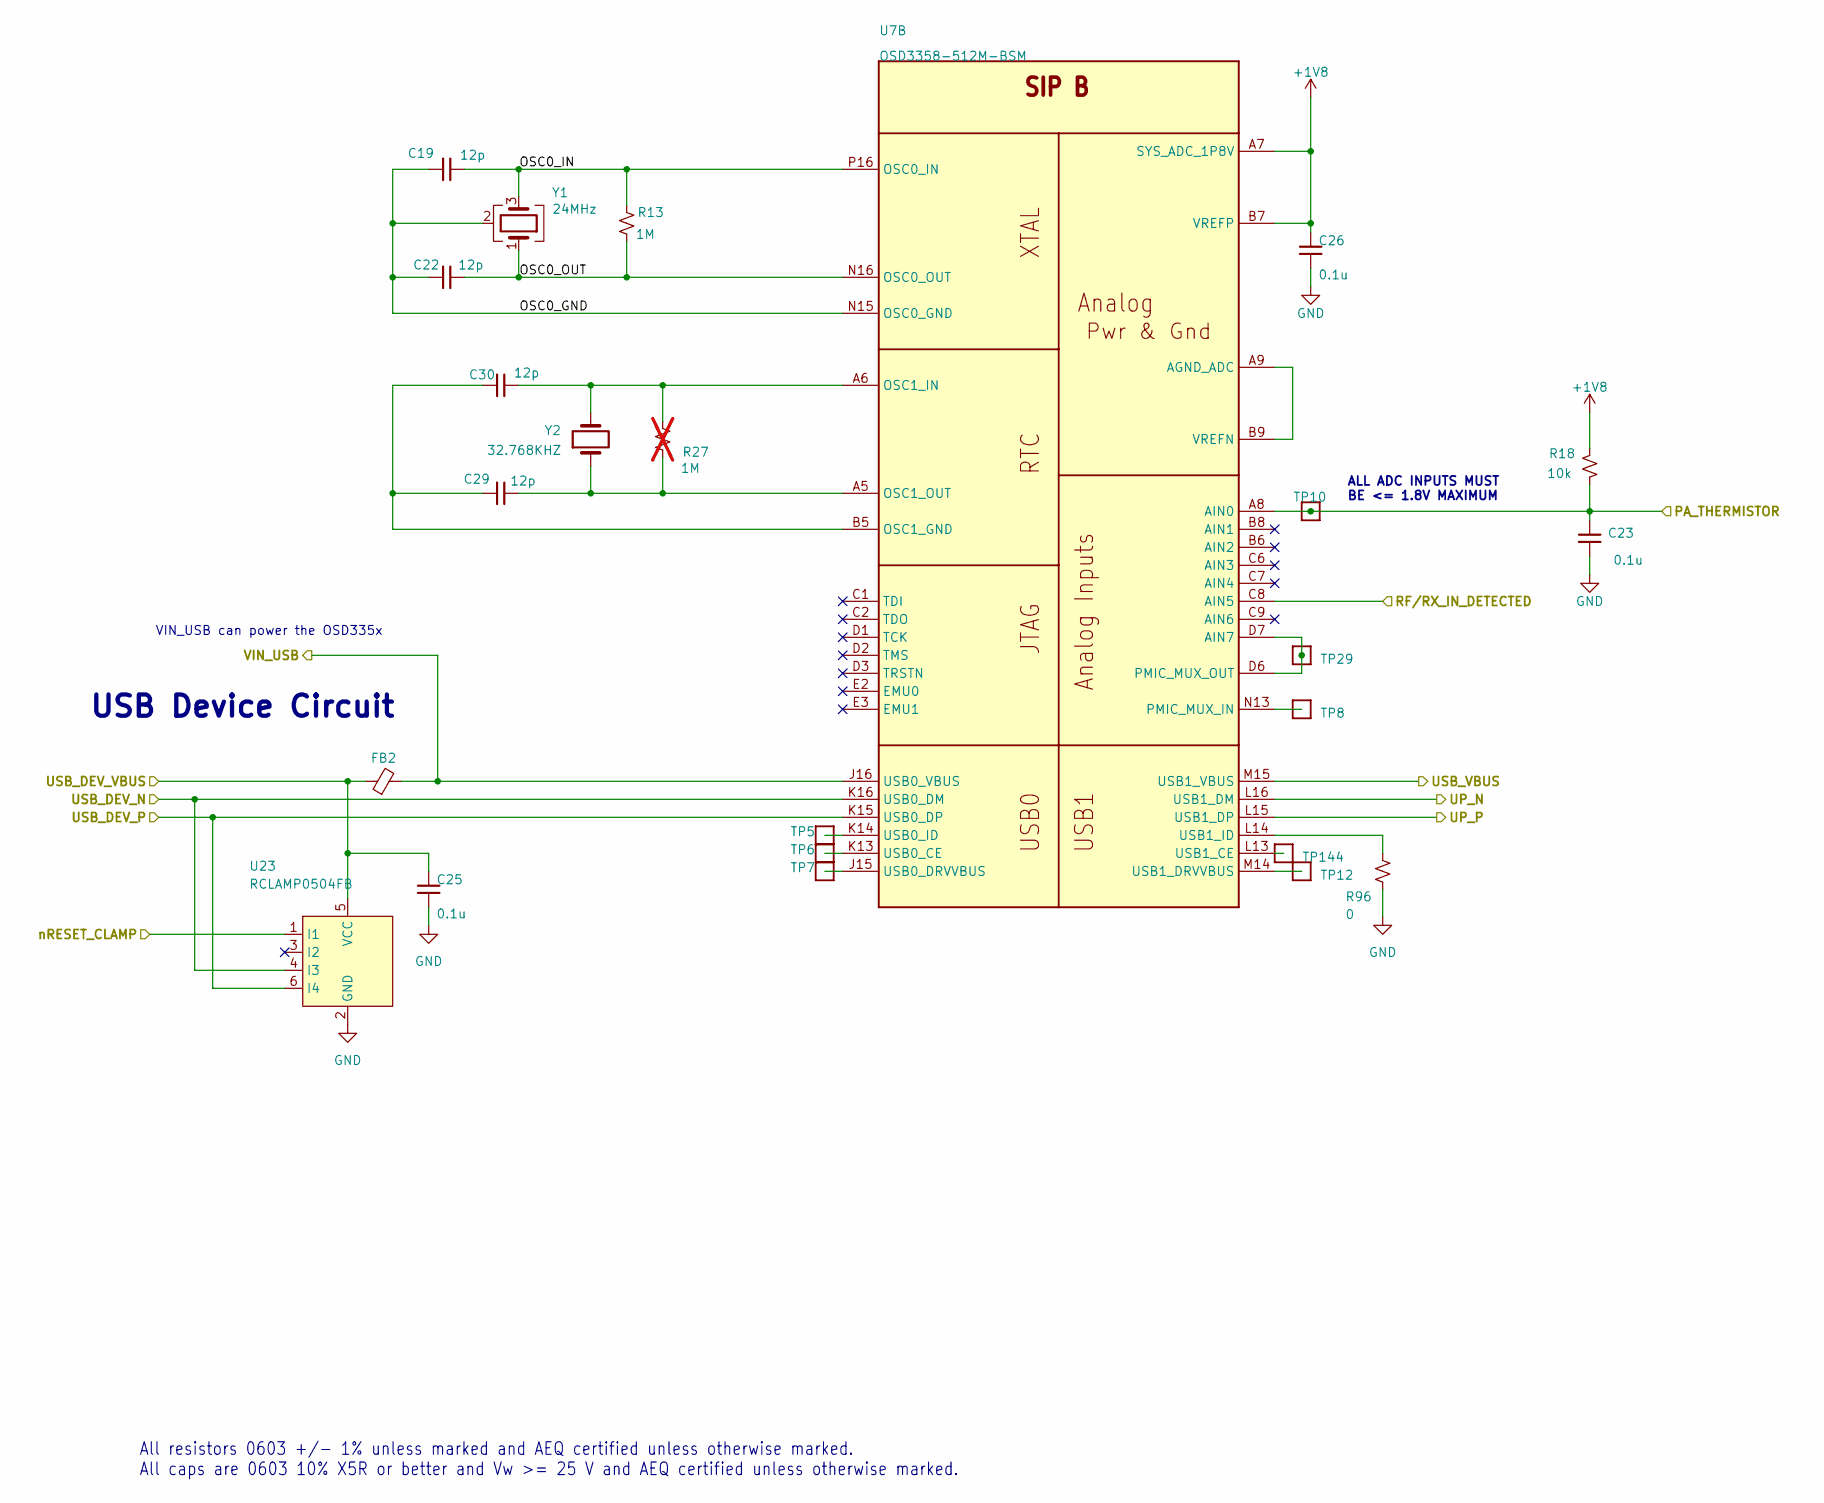
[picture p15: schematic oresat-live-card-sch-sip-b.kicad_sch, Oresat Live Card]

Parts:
C19, C22, C29, C30: 12p; 0603-C-NOSILK; MPN KAM15ACG2A120KT
C23, C25, C26: 0.1u; 0603-C-NOSILK; MPN C0603C104K5RACAUTO
FB2: BLM18KG300TH1D; 0603; MPN BLM18KG300JH1D
R13: 1M; 0603-C-NOSILK; MPN RMCF0603FT1M00
R18: 10k; 0603-C-NOSILK; MPN RMCF0603FT10K0
R27: 1M; R_0603_1608Metric; not fitted
R96: 0; 0603-C-NOSILK; MPN RMCF0603ZT0R00
TP5, TP6, TP7, TP12, TP144: TEST-POINT3X4; TestPoint_Pad_D1.0mm
TP8, TP10, TP29: TEST-POINT; TestPoint_Pad_D1.0mm
U7: OSD3358-512M-BSM; U-Octavo-OSD335X-BGA-256; MPN OSD3358-512M-BSM
U23: RCLAMP0504FB; SC70-6; MPN RCLAMP0504FBTCT
Y1: 24MHz; 5X3.2-4SMD; MPN ECS-240-12-30BQ-AEN-TR
Y2: 32.768KHZ; CRYSTAL_3.2X1.5; MPN ABS07-32.768KHZ-T

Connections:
+1V8: C26.1, R18.2, U7.A7 (SYS_ADC_1P8V), U7.B7 (VREFP)
/SIP A: Power/VIN_USB: FB2.2, U7.J16 (USB0_VBUS); also elsewhere on the board
/SIP A: Power/nRESET_CLAMP: U23.1 (I1); also elsewhere on the board
/SIP B: ADC + Crystals/OSC0_GND: C19.1, C22.1, U7.N15 (OSC0_GND), Y1.2 (G), Y1.4 (G)
/SIP B: ADC + Crystals/OSC0_IN: C19.2, R13.2, U7.P16 (OSC0_IN), Y1.3
/SIP B: ADC + Crystals/OSC0_OUT: C22.2, R13.1, U7.N16 (OSC0_OUT), Y1.1
/SIP B: ADC + Crystals/PA_THERMISTOR: C23.1, R18.1, TP10.1 (1_1), U7.A8 (AIN0); also elsewhere on the board
/SIP B: ADC + Crystals/RF/RX_IN_DETECTED: U7.C8 (AIN5); also elsewhere on the board
/SIP B: ADC + Crystals/UP_N: U7.L16 (USB1_DM); also elsewhere on the board
/SIP B: ADC + Crystals/UP_P: U7.L15 (USB1_DP); also elsewhere on the board
/SIP B: ADC + Crystals/USB_VBUS: U7.M15 (USB1_VBUS); also elsewhere on the board
/USB_DEV_N: U7.K16 (USB0_DM), U23.4 (I3); also elsewhere on the board
/USB_DEV_P: U7.K15 (USB0_DP), U23.6 (I4); also elsewhere on the board
/USB_DEV_VBUS: C25.1, FB2.1, U23.5 (VCC); also elsewhere on the board
GND: C23.2, C25.2, C26.2, R96.1, U23.2 (GND); also elsewhere on the board
unnamed: U7.A9 (AGND_ADC), U7.B9 (VREFN)
unnamed: TP29.1 (1_1), U7.D6 (PMIC_MUX_OUT), U7.D7 (AIN7)
unnamed: C29.2, C30.2, U7.B5 (OSC1_GND)
unnamed: C30.1, R27.2, U7.A6 (OSC1_IN), Y2.2
unnamed: C29.1, R27.1, U7.A5 (OSC1_OUT), Y2.1
unnamed: TP8.1 (1_1), U7.N13 (PMIC_MUX_IN)
unnamed: TP6.1 (1_1), U7.K13 (USB0_CE)
unnamed: TP7.1 (1_1), U7.J15 (USB0_DRVVBUS)
unnamed: TP5.1 (1_1), U7.K14 (USB0_ID)
unnamed: TP144.1 (1_1), U7.L13 (USB1_CE)
unnamed: TP12.1 (1_1), U7.M14 (USB1_DRVVBUS)
unnamed: R96.2, U7.L14 (USB1_ID)

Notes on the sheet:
USB Device Circuit
VIN_USB can power the OSD335x
All resistors 0603 +/- 1% unless marked and AEQ certified unless otherwise marked. All caps are 0603 10% X5R or better and Vw >= 25 V and AEQ certified unless otherwise marked.
ALL ADC INPUTS MUST BE <= 1.8V MAXIMUM

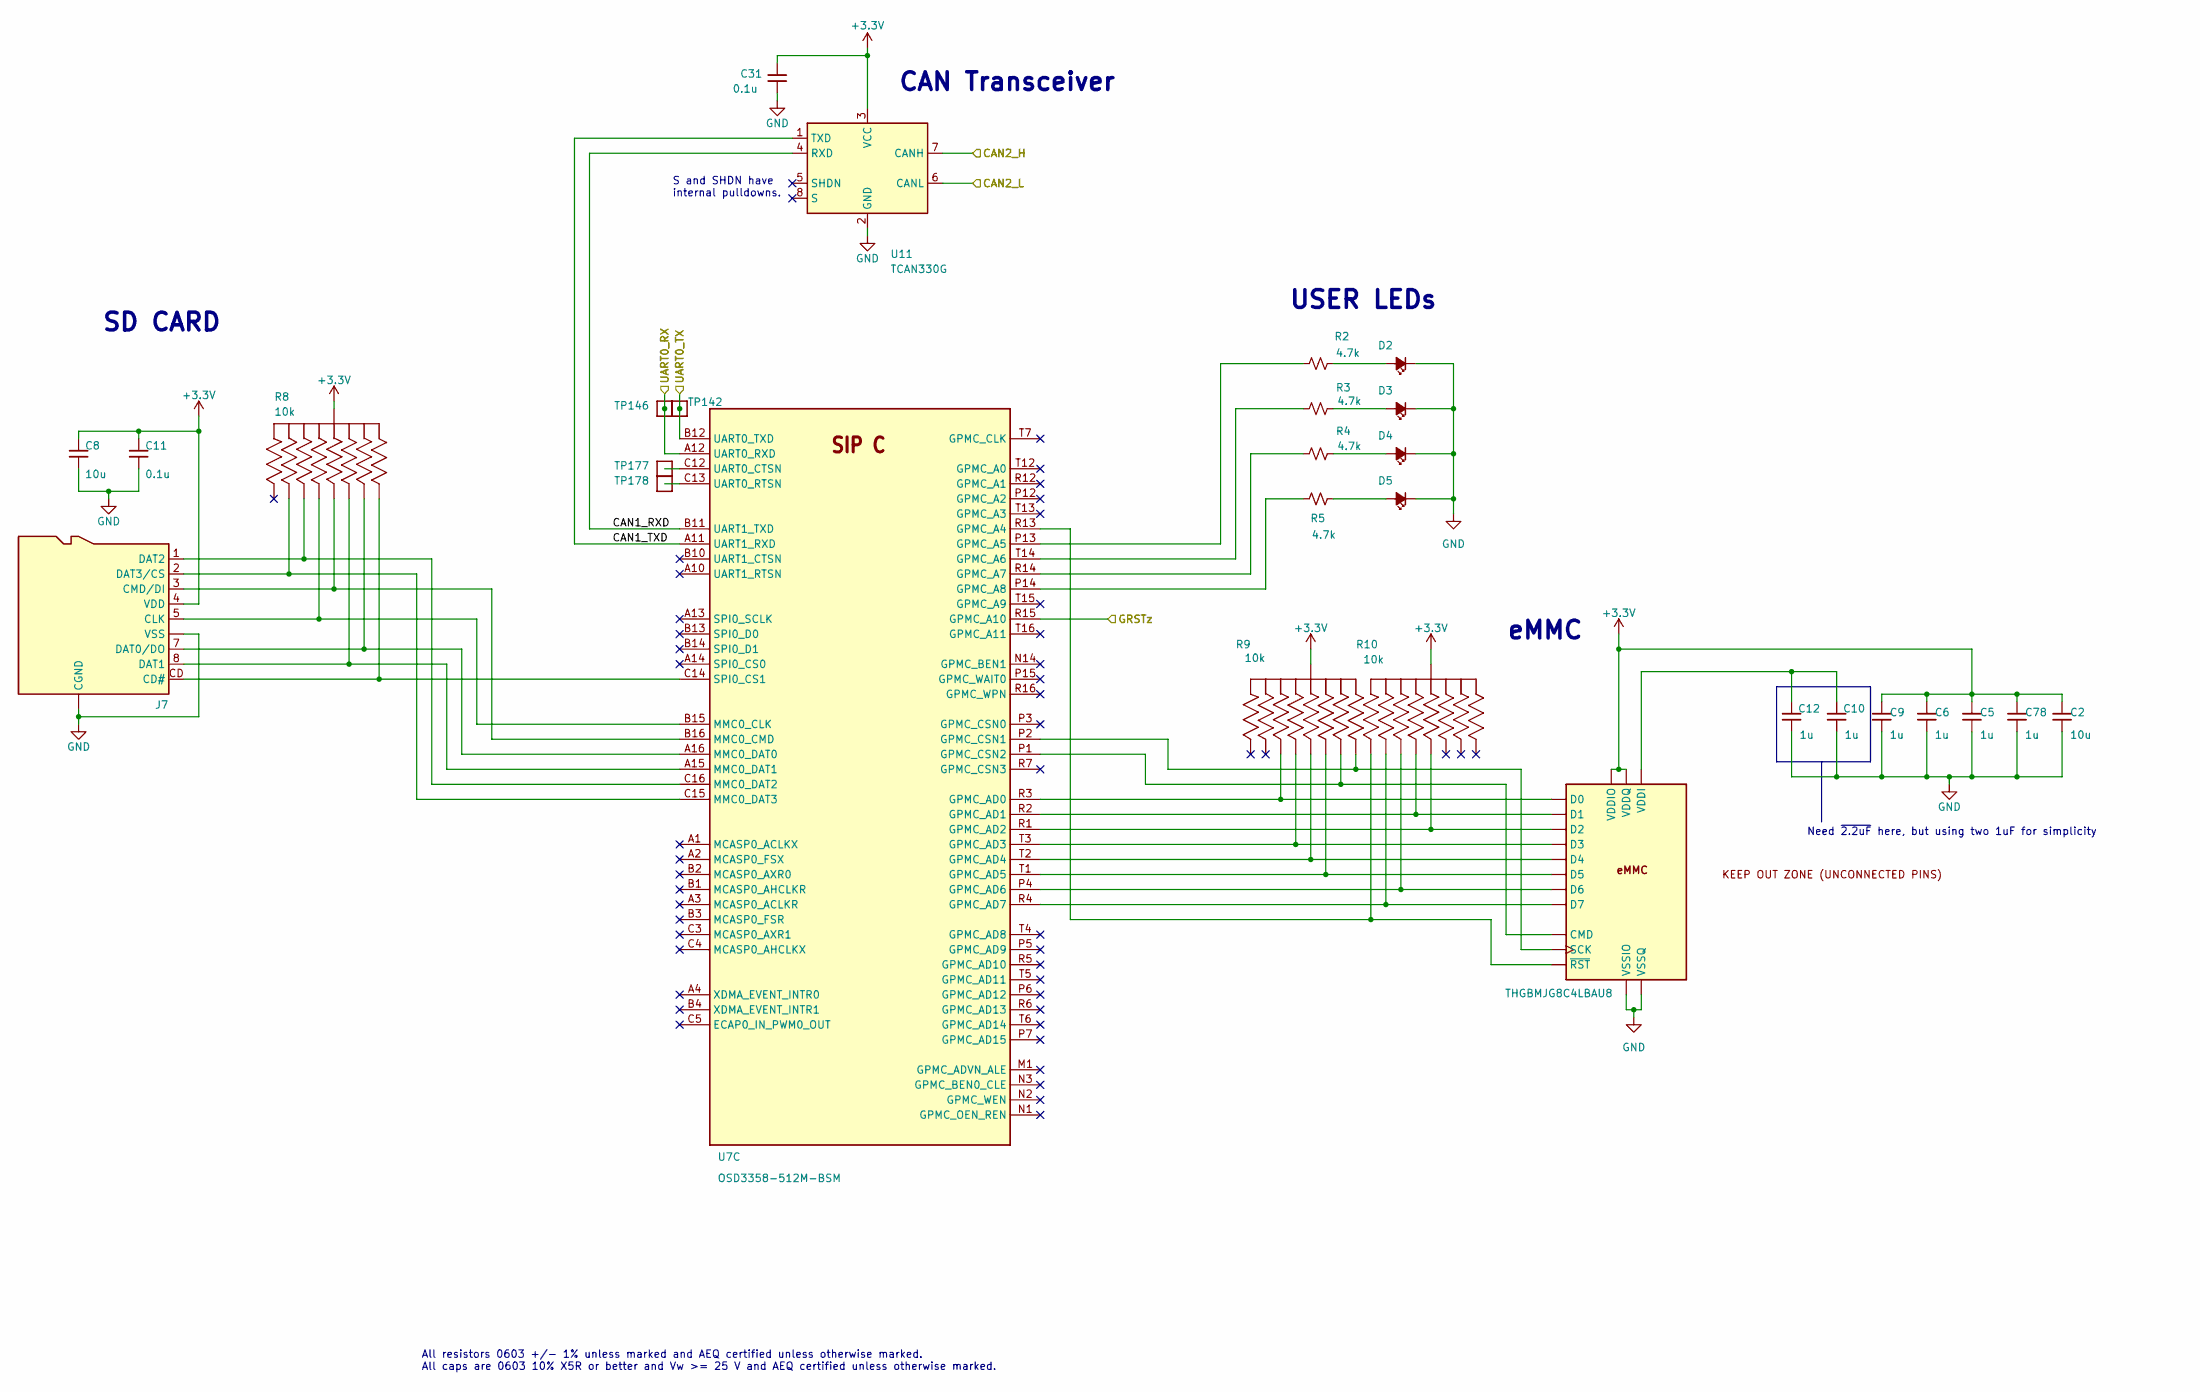
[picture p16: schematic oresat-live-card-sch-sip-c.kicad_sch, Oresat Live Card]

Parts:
C2, C8: 10u; 0805-C-NOSILK; MPN GRT21BC71E106KE13K
C5, C6, C9, C10, C12, C78: 1u; 0603-C-NOSILK; MPN GRT188R71E105KE13D
C11, C31: 0.1u; 0603-C-NOSILK; MPN C0603C104K5RACAUTO
D2, D3, D4, D5: BLU; LED-0603; MPN 150060BS75000
J7: DM3BT-DSF-PEJS; J-Hirose-DM3BT-DSF-PEJS; MPN DM3BT-DSF-PEJS
R2, R3, R4, R5: 4.7k; 0603-C-NOSILK; MPN RMCF0603FT4K70
R8, R9, R10: 10k; ARRAY_EXBA-M; MPN EXB-A10P103J
TP142, TP146: TEST-POINT3X4; TestPoint-0.75mm-th
TP177, TP178: TEST-POINT3X4; TestPoint_Pad_D1.0mm
U3: THGBMJG8C4LBAU8; BGA-153(11.5X13)(EMMC-BA); MPN THGBMJG8C4LBAU8
U7: OSD3358-512M-BSM; U-Octavo-OSD335X-BGA-256; MPN OSD3358-512M-BSM
U11: TCAN330G; SOT23-8_TI-DCN; MPN TCAN330GDCNR

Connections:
+3.3V: C2.1, C5.1, C6.1, C8.1, C9.1, C11.1, C31.2, C78.1, J7.4 (VDD), R8.5 (55), R8.10 (55), R9.5 (55), R9.10 (55), R10.5 (55), R10.10 (55), U3.C6 (VDDQ), U3.E6 (VDDIO), U3.F5 (VDDIO), U3.J10 (VDDIO), U3.K9 (VDDIO), U3.M4 (VDDQ), U3.N4 (VDDQ), U3.P3 (VDDQ), U3.P5 (VDDQ), U11.3 (VCC); also elsewhere on the board
/CAN2_H: U11.7 (CANH); also elsewhere on the board
/CAN2_L: U11.6 (CANL); also elsewhere on the board
/SIP C: SD + eMMC + CAN/CAN1_RXD: U7.B11 (UART1_TXD), U11.4 (RXD)
/SIP C: SD + eMMC + CAN/CAN1_TXD: U7.A11 (UART1_RXD), U11.1 (TXD)
/SIP C: SD + eMMC + CAN/GRSTz: U7.R15 (GPMC_A10); also elsewhere on the board
/UART0_RX: TP146.1 (1_1), U7.A12 (UART0_RXD); also elsewhere on the board
/UART0_TX: TP142.1 (1_1), U7.B12 (UART0_TXD); also elsewhere on the board
GND: C2.2, C5.2, C6.2, C8.2, C9.2, C10.2, C11.2, C12.2, C31.1, C78.2, D2.1 (K), D3.1 (K), D4.1 (K), D5.1 (K), J7.6 (VSS), J7.CGND1 (CGND), J7.CGND2 (CGND), J7.CGND3 (CGND), J7.CGND4 (CGND), J7.CGND5 (CGND), J7.CGND6 (CGND), J7.GND (VSS), U3.A6 (VSSIO), U3.C4 (VSSQ), U3.E7 (VSSIO), U3.G5 (VSSIO), U3.H10 (VSSIO), U3.J5 (VSSIO), U3.K8 (VSSIO), U3.N2 (VSSQ), U3.N5 (VSSQ), U3.P4 (VSSQ), U3.P6 (VSSQ), U11.2 (GND); also elsewhere on the board
unnamed: D2.2 (A), R2.2
unnamed: D3.2 (A), R3.2
unnamed: D4.2 (A), R4.2
unnamed: D5.2 (A), R5.2
unnamed: J7.CD (CD#), R8.6 (66), U7.C14 (SPI0_CS1)
unnamed: J7.5 (CLK), R8.8 (88), U7.B15 (MMC0_CLK)
unnamed: J7.3 (CMD/DI), R8.3 (33), U7.B16 (MMC0_CMD)
unnamed: J7.7 (DAT0/DO), R8.4 (44), U7.A16 (MMC0_DAT0)
unnamed: J7.8 (DAT1), R8.7 (77), U7.A15 (MMC0_DAT1)
unnamed: J7.1 (DAT2), R8.2 (22), U7.C16 (MMC0_DAT2)
unnamed: J7.2 (DAT3/CS), R8.9 (99), U7.C15 (MMC0_DAT3)
unnamed: R9.2 (22), U3.A3 (D0), U7.R3 (GPMC_AD0)
unnamed: R9.3 (33), U3.B3 (D4), U7.T2 (GPMC_AD4)
unnamed: R9.4 (44), U3.M5 (CMD), U7.P1 (GPMC_CSN2)
unnamed: R9.6 (66), U3.M6 (SCK), U7.P2 (GPMC_CSN1)
unnamed: R9.7 (77), U3.B4 (D5), U7.T1 (GPMC_AD5)
unnamed: R9.8 (88), U3.B2 (D3), U7.T3 (GPMC_AD3)
unnamed: R10.1 (11), U3.K5 (~RST), U7.R13 (GPMC_A4)
unnamed: R10.2 (22), U3.B5 (D6), U7.P4 (GPMC_AD6)
unnamed: R10.3 (33), U3.A5 (D2), U7.R1 (GPMC_AD2)
unnamed: R10.8 (88), U3.A4 (D1), U7.R2 (GPMC_AD1)
unnamed: R10.9 (99), U3.B6 (D7), U7.R4 (GPMC_AD7)
unnamed: C10.1, C12.1, U3.C2 (VDDI)
unnamed: R2.1, U7.P13 (GPMC_A5)
unnamed: R3.1, U7.T14 (GPMC_A6)
unnamed: R4.1, U7.R14 (GPMC_A7)
unnamed: R5.1, U7.P14 (GPMC_A8)
unnamed: TP177.1 (1_1), U7.C12 (UART0_CTSN)
unnamed: TP178.1 (1_1), U7.C13 (UART0_RTSN)

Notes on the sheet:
CAN Transceiver
USER LEDs
S and SHDN have internal pulldowns.
Need ~{2.2uF} here, but using two 1uF for simplicity
All resistors 0603 +/- 1% unless marked and AEQ certified unless otherwise marked. All caps are 0603 10% X5R or better and Vw >= 25 V and AEQ certified unless otherwise marked.
eMMC
SD CARD

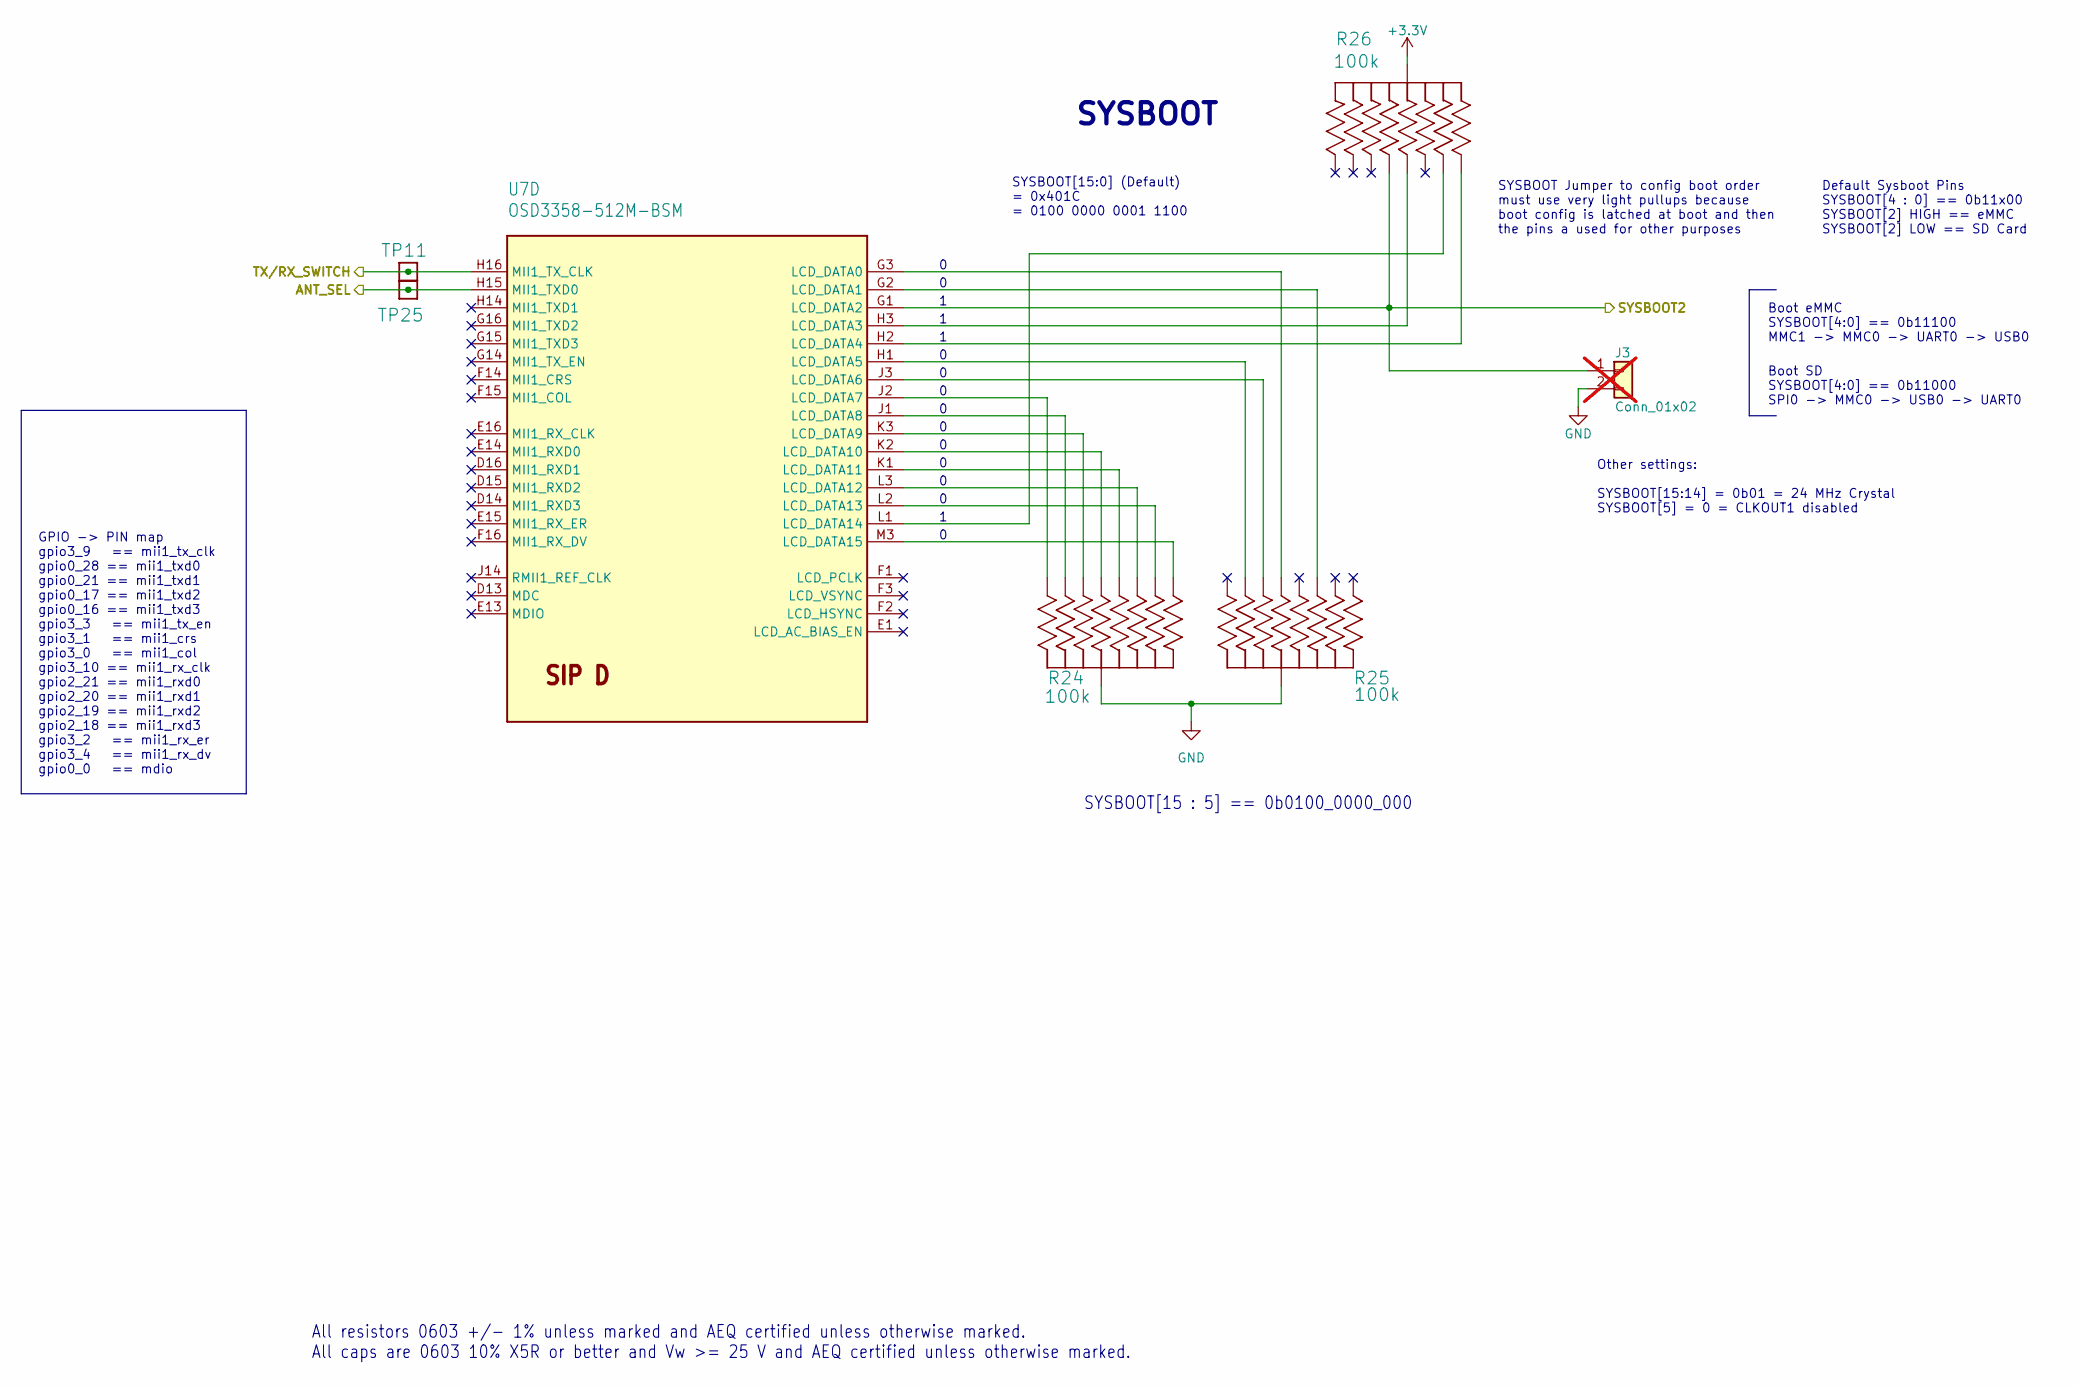
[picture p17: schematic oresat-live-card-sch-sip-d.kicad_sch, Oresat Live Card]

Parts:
J3: Conn_01x02; PinHeader_1x02_P2.54mm_Vertical; not fitted
R24, R25, R26: 100k; ARRAY_EXBA-M; MPN EXB-A10P104J
TP11, TP25: TEST-POINT3X4; TestPoint_Pad_D1.0mm
U7: OSD3358-512M-BSM; U-Octavo-OSD335X-BGA-256; MPN OSD3358-512M-BSM

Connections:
+3.3V: R26.5 (55), R26.10 (55); also elsewhere on the board
/Power + OPD/SYSBOOT2: J3.1, R26.8 (88), U7.G1 (LCD_DATA2); also elsewhere on the board
/SIP D: Boot/ANT_SEL: TP25.1 (1_1), U7.H15 (MII1_TXD0); also elsewhere on the board
/SIP D: Boot/TX/RX_SWITCH: TP11.1 (1_1), U7.H16 (MII1_TX_CLK); also elsewhere on the board
GND: J3.2, R24.5 (55), R24.10 (55), R25.5 (55), R25.10 (55); also elsewhere on the board
unnamed: R24.1 (11), U7.M3 (LCD_DATA15)
unnamed: R24.2 (22), U7.L3 (LCD_DATA12)
unnamed: R24.3 (33), U7.K2 (LCD_DATA10)
unnamed: R24.4 (44), U7.J1 (LCD_DATA8)
unnamed: R24.6 (66), U7.J2 (LCD_DATA7)
unnamed: R24.7 (77), U7.K3 (LCD_DATA9)
unnamed: R24.8 (88), U7.K1 (LCD_DATA11)
unnamed: R24.9 (99), U7.L2 (LCD_DATA13)
unnamed: R25.2 (22), U7.G2 (LCD_DATA1)
unnamed: R25.3 (33), U7.G3 (LCD_DATA0)
unnamed: R25.4 (44), U7.H1 (LCD_DATA5)
unnamed: R25.7 (77), U7.J3 (LCD_DATA6)
unnamed: R26.3 (33), U7.H3 (LCD_DATA3)
unnamed: R26.4 (44), U7.L1 (LCD_DATA14)
unnamed: R26.6 (66), U7.H2 (LCD_DATA4)

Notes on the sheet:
All resistors 0603 +/- 1% unless marked and AEQ certified unless otherwise marked. All caps are 0603 10% X5R or better and Vw >= 25 V and AEQ certified unless otherwise marked.
Boot eMMC SYSBOOT[4:0] == 0b11100 MMC1 -> MMC0 -> UART0 -> USB0
GPIO -> PIN map gpio3_9 == mii1_tx_clk gpio0_28 == mii1_txd0 gpio0_21 == mii1_txd1 gpio0_17 == mii1_txd2 gpio0_16 == mii1_txd3 gpio3_3 == mii1_tx_en gpio3_1 == mii1_crs gpio3_0 == mii1_col gpio3_10 == mii1_rx_clk gpio2_21 == mii1_rxd0 gpio2_20 == mii1_rxd1 gpio2_19 == mii1_rxd2 gpio2_18 == mii1_rxd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
Boot SD SYSBOOT[4:0] == 0b11000 SPI0 -> MMC0 -> USB0 -> UART0
SYSBOOT[15 : 5] == 0b0100_0000_000
SYSBOOT Jumper to config boot order must use very light pullups because boot config is latched at boot and then the pins a used for other purposes
Other settings: SYSBOOT[15:14] = 0b01 = 24 MHz Crystal SYSBOOT[5] = 0 = CLKOUT1 disabled
SYSBOOT
Default Sysboot Pins SYSBOOT[4 : 0] == 0b11x00 SYSBOOT[2] HIGH == eMMC SYSBOOT[2] LOW == SD Card
SYSBOOT[15:0] (Default) = 0x401C = 0100 0000 0001 1100

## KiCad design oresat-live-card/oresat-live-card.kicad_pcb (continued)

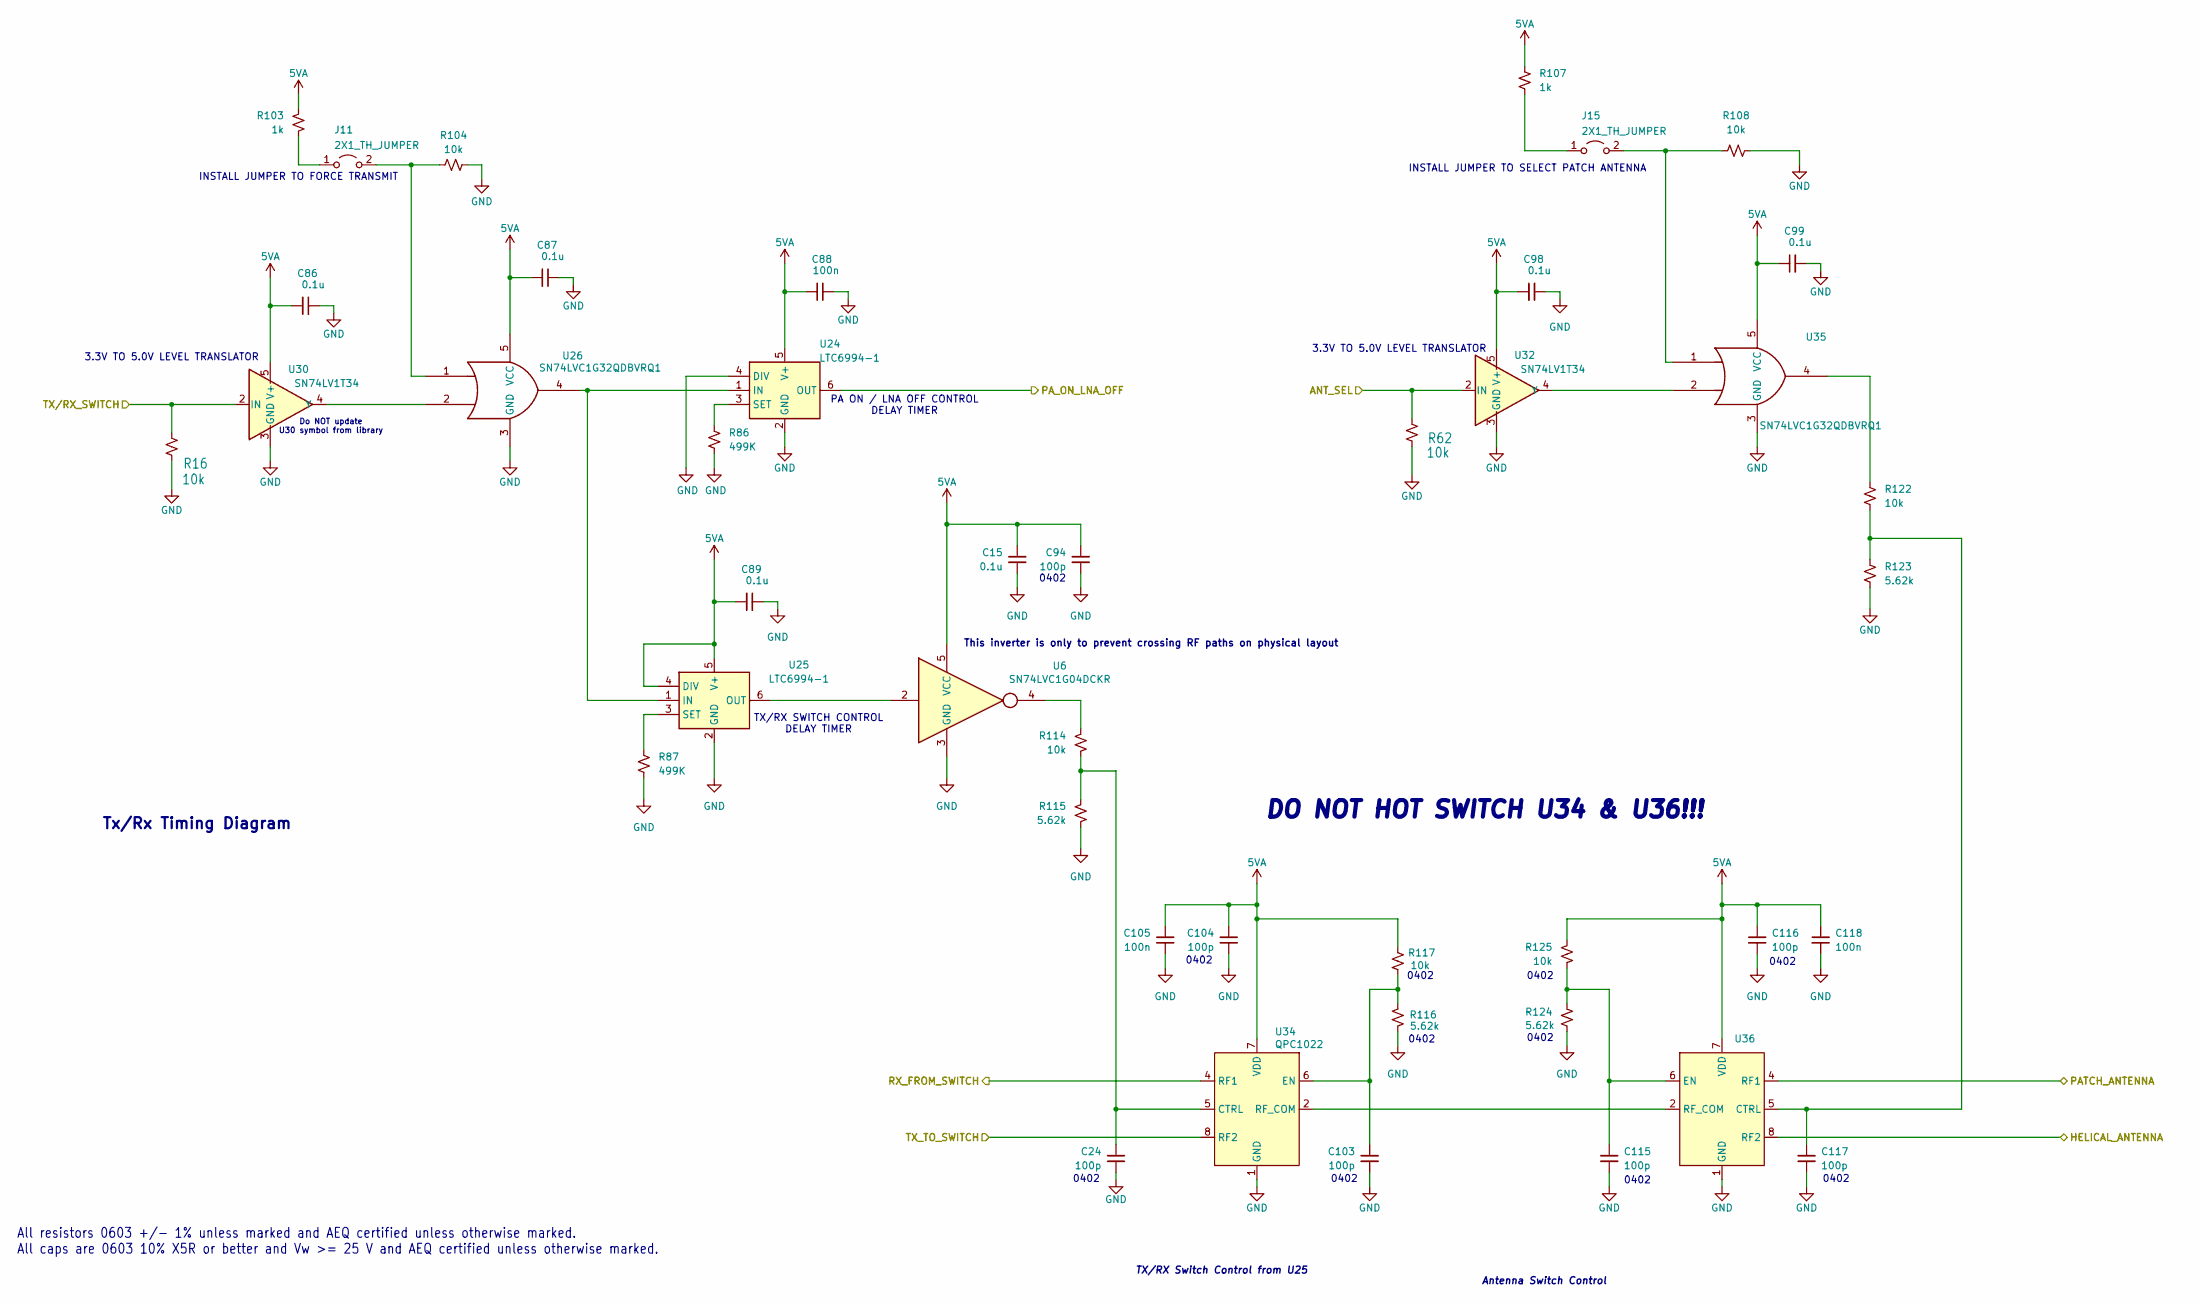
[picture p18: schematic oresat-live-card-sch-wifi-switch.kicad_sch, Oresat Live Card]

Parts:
C15, C86, C87, C89, C98, C99: 0.1u; 0603-C-NOSILK; MPN C0603C104K5RACAUTO
C24, C94, C103, C104, C115, C116, C117: 100p; 0402-C-NOSILK; MPN GCM1555C1H101GA16D
C88, C105, C118: 100n; 0603-C-NOSILK; MPN CGA3E2X7R1E104K080AA
J11, J15: 2X1_TH_JUMPER; 2X1; MPN XGL4020-332MEC
R16, R62, R104, R108, R114, R122: 10k; 0603-C-NOSILK; MPN RMCF0603FT10K0
R86, R87: 499K; 0603-C-NOSILK; MPN ERJ-U03F4993V
R103, R107: 1k; 0603-C-NOSILK; MPN RMCF0603FT1K00
R115, R123: 5.62k; 0603-C-NOSILK; MPN ERJ-3EKF5621V
R116, R124: 5.62k; 0402-C-NOSILK; MPN ERJ-2RKF5621X
R117, R125: 10k; 0402-C-NOSILK; MPN ERJ-2RKF1002X
U6: SN74LVC1G04DCKR; C70(TI-DCK); MPN SN74LVC1G04DCKR
U24, U25: LTC6994-1; TSOT-23-6; MPN LTC6994IS6-1#TRPBF
U26, U35: SN74LVC1G32QDBVRQ1; SOT-23-5; MPN SN74LVC1G32QDBVRQ1
U30, U32: SN74LV1T34; SOT-353_SC-70-5; MPN SN74LV1T34QDCKRQ1
U34, U36: QPC1022; MPN QPC1022TR7

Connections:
5VA: C15.1, C86.1, C87.1, C88.1, C89.1, C94.1, C98.1, C99.1, C104.1, C105.1, C116.1, C118.1, R103.1, R107.1, R117.1, R125.2, U6.5 (VCC), U24.5 (V+), U25.4 (DIV), U25.5 (V+), U26.5 (VCC), U30.5 (V+), U32.5 (V+), U34.7 (VDD), U35.5 (VCC), U36.7 (VDD); also elsewhere on the board
/HEL_ANT: U36.8 (RF2); also elsewhere on the board
/PATCH_ANT: U36.4 (RF1); also elsewhere on the board
/SIP D: Boot/ANT_SEL: R62.2, U32.2 (IN); also elsewhere on the board
/SIP D: Boot/TX/RX_SWITCH: R16.2, U30.2 (IN); also elsewhere on the board
/WiFi LNA/LNA_SHUTDOWN: U24.6 (OUT); also elsewhere on the board
/WiFi LNA/RX_FROM_SWITCH: U34.4 (RF1); also elsewhere on the board
/WiFi PA/TX_TO_SWITCH: U34.8 (RF2); also elsewhere on the board
GND: C15.2, C24.2, C86.2, C87.2, C88.2, C89.2, C94.2, C98.2, C99.2, C103.2, C104.2, C105.2, C115.2, C116.2, C117.2, C118.2, R16.1, R62.1, R86.2, R87.2, R104.2, R108.2, R115.2, R116.2, R123.1, R124.1, U6.3 (GND), U24.2 (GND), U24.4 (DIV), U25.2 (GND), U26.3 (GND), U30.3 (GND), U32.3 (GND), U34.1 (GND), U34.3 (GND), U34.9 (GND), U35.3 (GND), U36.1 (GND), U36.3 (GND), U36.9 (GND); also elsewhere on the board
unnamed: J11.1 (A), R103.2
unnamed: J11.2 (B), R104.1, U26.1
unnamed: J15.1 (A), R107.2
unnamed: J15.2 (B), R108.1, U35.1
unnamed: R114.2, U6.4
unnamed: R122.1, U35.4
unnamed: U24.1 (IN), U25.1 (IN), U26.4
unnamed: R86.1, U24.3 (SET)
unnamed: U6.2, U25.6 (OUT)
unnamed: R87.1, U25.3 (SET)
unnamed: U26.2, U30.4 (Y)
unnamed: U32.4 (Y), U35.2
unnamed: C24.1, R114.1, R115.1, U34.5 (CTRL)
unnamed: C103.1, R116.1, R117.2, U34.6 (EN)
unnamed: U34.2 (RF_COM), U36.2 (RF_COM)
unnamed: C117.1, R122.2, R123.2, U36.5 (CTRL)
unnamed: C115.1, R124.2, R125.1, U36.6 (EN)

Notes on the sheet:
DO NOT HOT SWITCH U34 & U36!!!
3.3V TO 5.0V LEVEL TRANSLATOR
0402
This inverter is only to prevent crossing RF paths on physical layout
Tx/Rx Timing Diagram
INSTALL JUMPER TO SELECT PATCH ANTENNA
Do NOT update U30 symbol from library
TX/RX SWITCH CONTROL DELAY TIMER
All resistors 0603 +/- 1% unless marked and AEQ certified unless otherwise marked. All caps are 0603 10% X5R or better and Vw >= 25 V and AEQ certified unless otherwise marked.
Antenna Switch Control
PA ON / LNA OFF CONTROL DELAY TIMER
INSTALL JUMPER TO FORCE TRANSMIT
3.3V TO 5.0V LEVEL TRANSLATOR
TX/RX Switch Control from U25

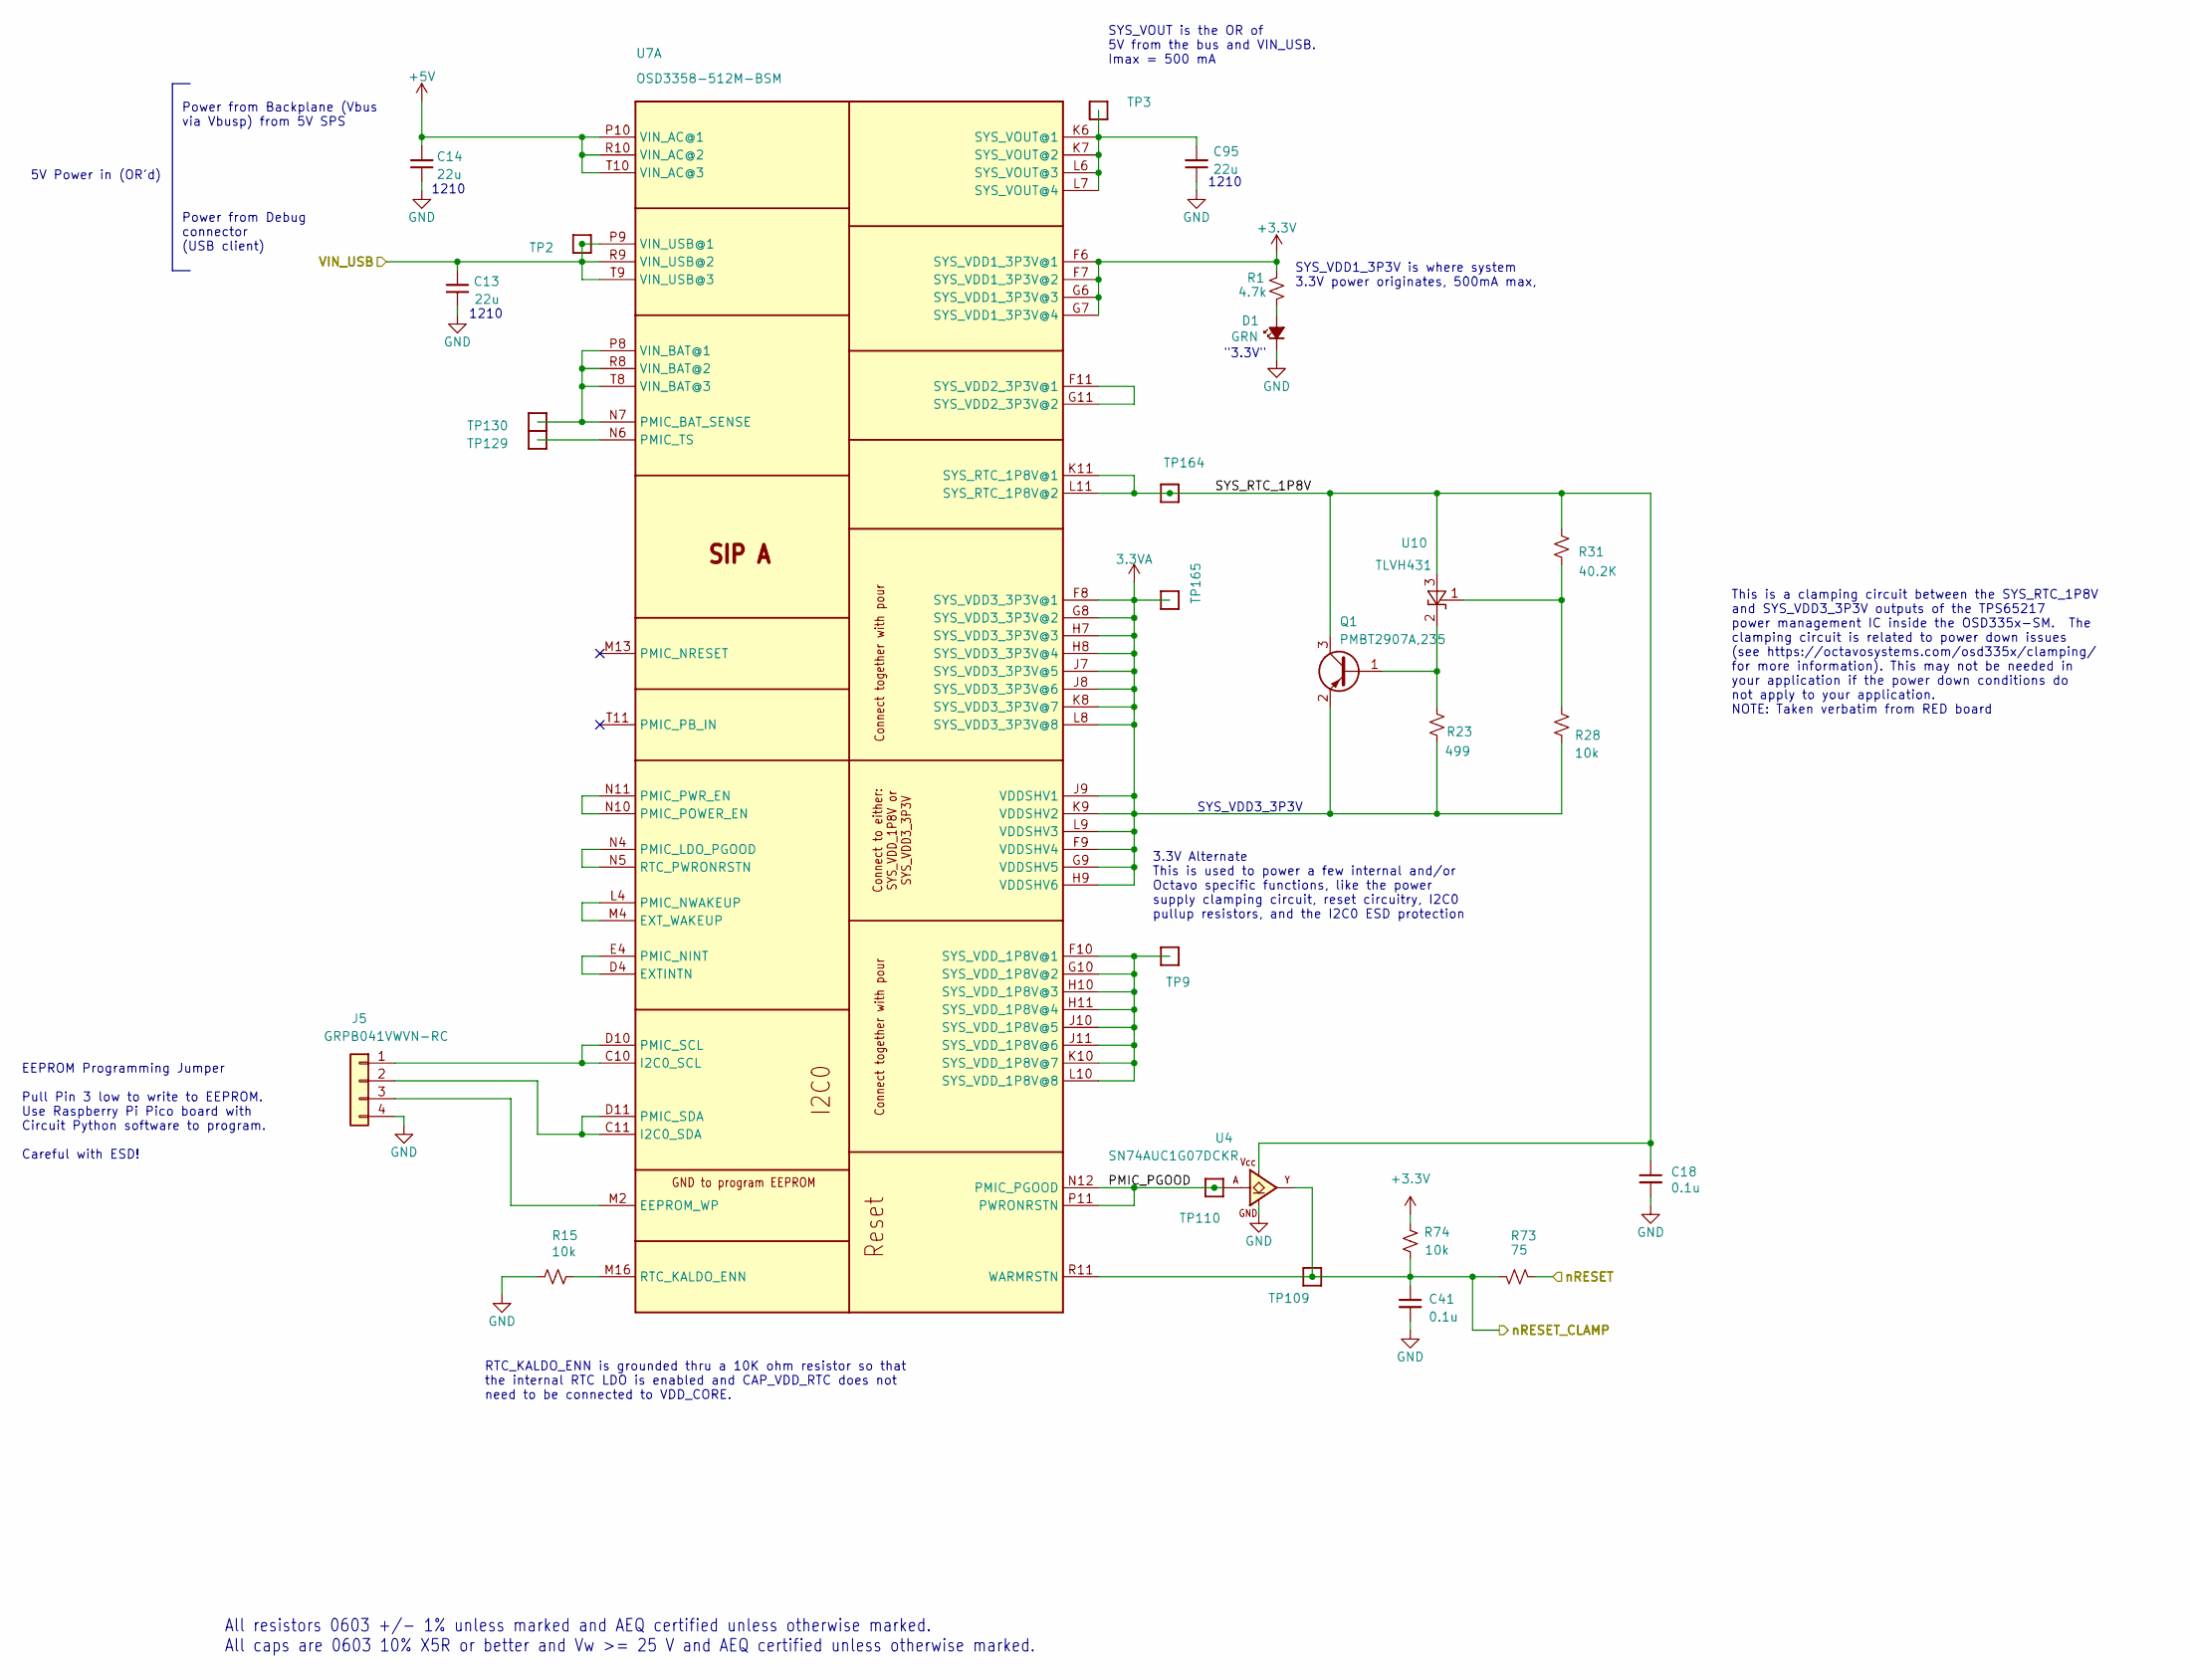
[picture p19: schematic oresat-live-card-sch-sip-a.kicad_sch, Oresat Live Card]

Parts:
C13, C14, C95: 22u; C_1210_3225Metric; MPN TMK325B7226KMHP
C18, C41: 0.1u; 0603-C-NOSILK; MPN C0603C104K5RACAUTO
D1: GRN; LED-0603; MPN 150060GS75000
J5: GRPB041VWVN-RC; PinHeader_1x04_P1.27mm_Vertical; MPN GRPB041VWVN-RC
Q1: PMBT2907A,235; SOT-23; MPN PMBT2907A,235
R1: 4.7k; 0603-C-NOSILK; MPN RMCF0603FT4K70
R15, R28, R74: 10k; 0603-C-NOSILK; MPN RMCF0603FT10K0
R23: 499; 0603-C-NOSILK; MPN RMCF0603FT499R
R31: 40.2K; 0603-C-NOSILK; MPN RMCF0603FG40K2
R73: 75; 0603-C-NOSILK; MPN RMCF0603FT75R0
TP2, TP3, TP9, TP109, TP110, TP129, TP130, TP164, TP165: TEST-POINT3X4; TestPoint_Pad_D1.0mm
U4: SN74AUC1G07DCKR; C70(TI-DCK); MPN SN74AUC1G07DCKR
U7: OSD3358-512M-BSM; U-Octavo-OSD335X-BGA-256; MPN OSD3358-512M-BSM
U10: TLVH431; SOT23-3; MPN TLVH431BQDBZRQ1

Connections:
3.3VA: Q1.2 (E), R23.2, R28.2, TP165.1 (1_1), U7.F8 (SYS_VDD3_3P3V@1), U7.F9 (VDDSHV4), U7.G8 (SYS_VDD3_3P3V@2), U7.G9 (VDDSHV5), U7.H7 (SYS_VDD3_3P3V@3), U7.H8 (SYS_VDD3_3P3V@4), U7.H9 (VDDSHV6), U7.J7 (SYS_VDD3_3P3V@5), U7.J8 (SYS_VDD3_3P3V@6), U7.J9 (VDDSHV1), U7.K8 (SYS_VDD3_3P3V@7), U7.K9 (VDDSHV2), U7.L8 (SYS_VDD3_3P3V@8), U7.L9 (VDDSHV3)
+3.3V: R1.1, R74.2, U7.F6 (SYS_VDD1_3P3V@1), U7.F7 (SYS_VDD1_3P3V@2), U7.G6 (SYS_VDD1_3P3V@3), U7.G7 (SYS_VDD1_3P3V@4); also elsewhere on the board
+5V: C14.1, U7.P10 (VIN_AC@1), U7.R10 (VIN_AC@2), U7.T10 (VIN_AC@3); also elsewhere on the board
/SIP A: Power/PMIC_PGOOD: TP110.1 (1_1), U4.2 (A), U7.N12 (PMIC_PGOOD), U7.P11 (PWRONRSTN)
/SIP A: Power/SYS_RTC_1P8V: C18.1, Q1.3 (C), R31.1, TP164.1 (1_1), U4.5 (VCC), U7.K11 (SYS_RTC_1P8V@1), U7.L11 (SYS_RTC_1P8V@2), U10.3 (A)
/SIP A: Power/VIN_USB: C13.1, TP2.1 (1_1), U7.P9 (VIN_USB@1), U7.R9 (VIN_USB@2), U7.T9 (VIN_USB@3); also elsewhere on the board
/SIP A: Power/nRESET_CLAMP: C41.1, R73.2, R74.1, TP109.1 (1_1), U4.4 (Y), U7.R11 (WARMRSTN); also elsewhere on the board
/nRESET: R73.1; also elsewhere on the board
GND: C13.2, C14.2, C18.2, C41.2, C95.2, D1.1 (K), J5.4, R15.1, U4.3 (GND); also elsewhere on the board
unnamed: D1.2 (A), R1.2
unnamed: J5.1, U7.C10 (I2C0_SCL), U7.D10 (PMIC_SCL)
unnamed: J5.2, U7.C11 (I2C0_SDA), U7.D11 (PMIC_SDA)
unnamed: J5.3, U7.M2 (EEPROM_WP)
unnamed: Q1.1 (B), R23.1, U10.2 (K)
unnamed: U7.D4 (EXTINTN), U7.E4 (PMIC_NINT)
unnamed: U7.L4 (PMIC_NWAKEUP), U7.M4 (EXT_WAKEUP)
unnamed: TP130.1 (1_1), U7.N7 (PMIC_BAT_SENSE), U7.P8 (VIN_BAT@1), U7.R8 (VIN_BAT@2), U7.T8 (VIN_BAT@3)
unnamed: U7.N4 (PMIC_LDO_PGOOD), U7.N5 (RTC_PWRONRSTN)
unnamed: U7.N10 (PMIC_POWER_EN), U7.N11 (PMIC_PWR_EN)
unnamed: TP129.1 (1_1), U7.N6 (PMIC_TS)
unnamed: R15.2, U7.M16 (RTC_KALDO_ENN)
unnamed: U7.F11 (SYS_VDD2_3P3V@1), U7.G11 (SYS_VDD2_3P3V@2)
unnamed: TP9.1 (1_1), U7.F10 (SYS_VDD_1P8V@1), U7.G10 (SYS_VDD_1P8V@2), U7.H10 (SYS_VDD_1P8V@3), U7.H11 (SYS_VDD_1P8V@4), U7.J10 (SYS_VDD_1P8V@5), U7.J11 (SYS_VDD_1P8V@6), U7.K10 (SYS_VDD_1P8V@7), U7.L10 (SYS_VDD_1P8V@8)
unnamed: C95.1, TP3.1 (1_1), U7.K6 (SYS_VOUT@1), U7.K7 (SYS_VOUT@2), U7.L6 (SYS_VOUT@3), U7.L7 (SYS_VOUT@4)
unnamed: R28.1, R31.2, U10.1 (REF)

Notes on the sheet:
Power from Backplane (Vbus via Vbusp) from 5V SPS
All resistors 0603 +/- 1% unless marked and AEQ certified unless otherwise marked. All caps are 0603 10% X5R or better and Vw >= 25 V and AEQ certified unless otherwise marked.
SYS_VOUT is the OR of 5V from the bus and VIN_USB. Imax = 500 mA
EEPROM Programming Jumper Pull Pin 3 low to write to EEPROM. Use Raspberry Pi Pico board with Circuit Python software to program. Careful with ESD!
"3.3V"
5V Power in (OR'd)
RTC_KALDO_ENN is grounded thru a 10K ohm resistor so that the internal RTC LDO is enabled and CAP_VDD_RTC does not need to be connected to VDD_CORE.
SYS_VDD1_3P3V is where system 3.3V power originates, 500mA max,
Power from Debug connector (USB client)
This is a clamping circuit between the SYS_RTC_1P8V and SYS_VDD3_3P3V outputs of the TPS65217 power management IC inside the OSD335x-SM. The clamping circuit is related to power down issues (see https://octavosystems.com/osd335x/clamping/ for more information). This may not be needed in your applic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
1210
SYS_VDD3_3P3V
3.3V Alternate This is used to power a few internal and/or Octavo specific functions, like the power supply clamping circuit, reset circuitry, I2C0 pullup resistors, and the I2C0 ESD protection

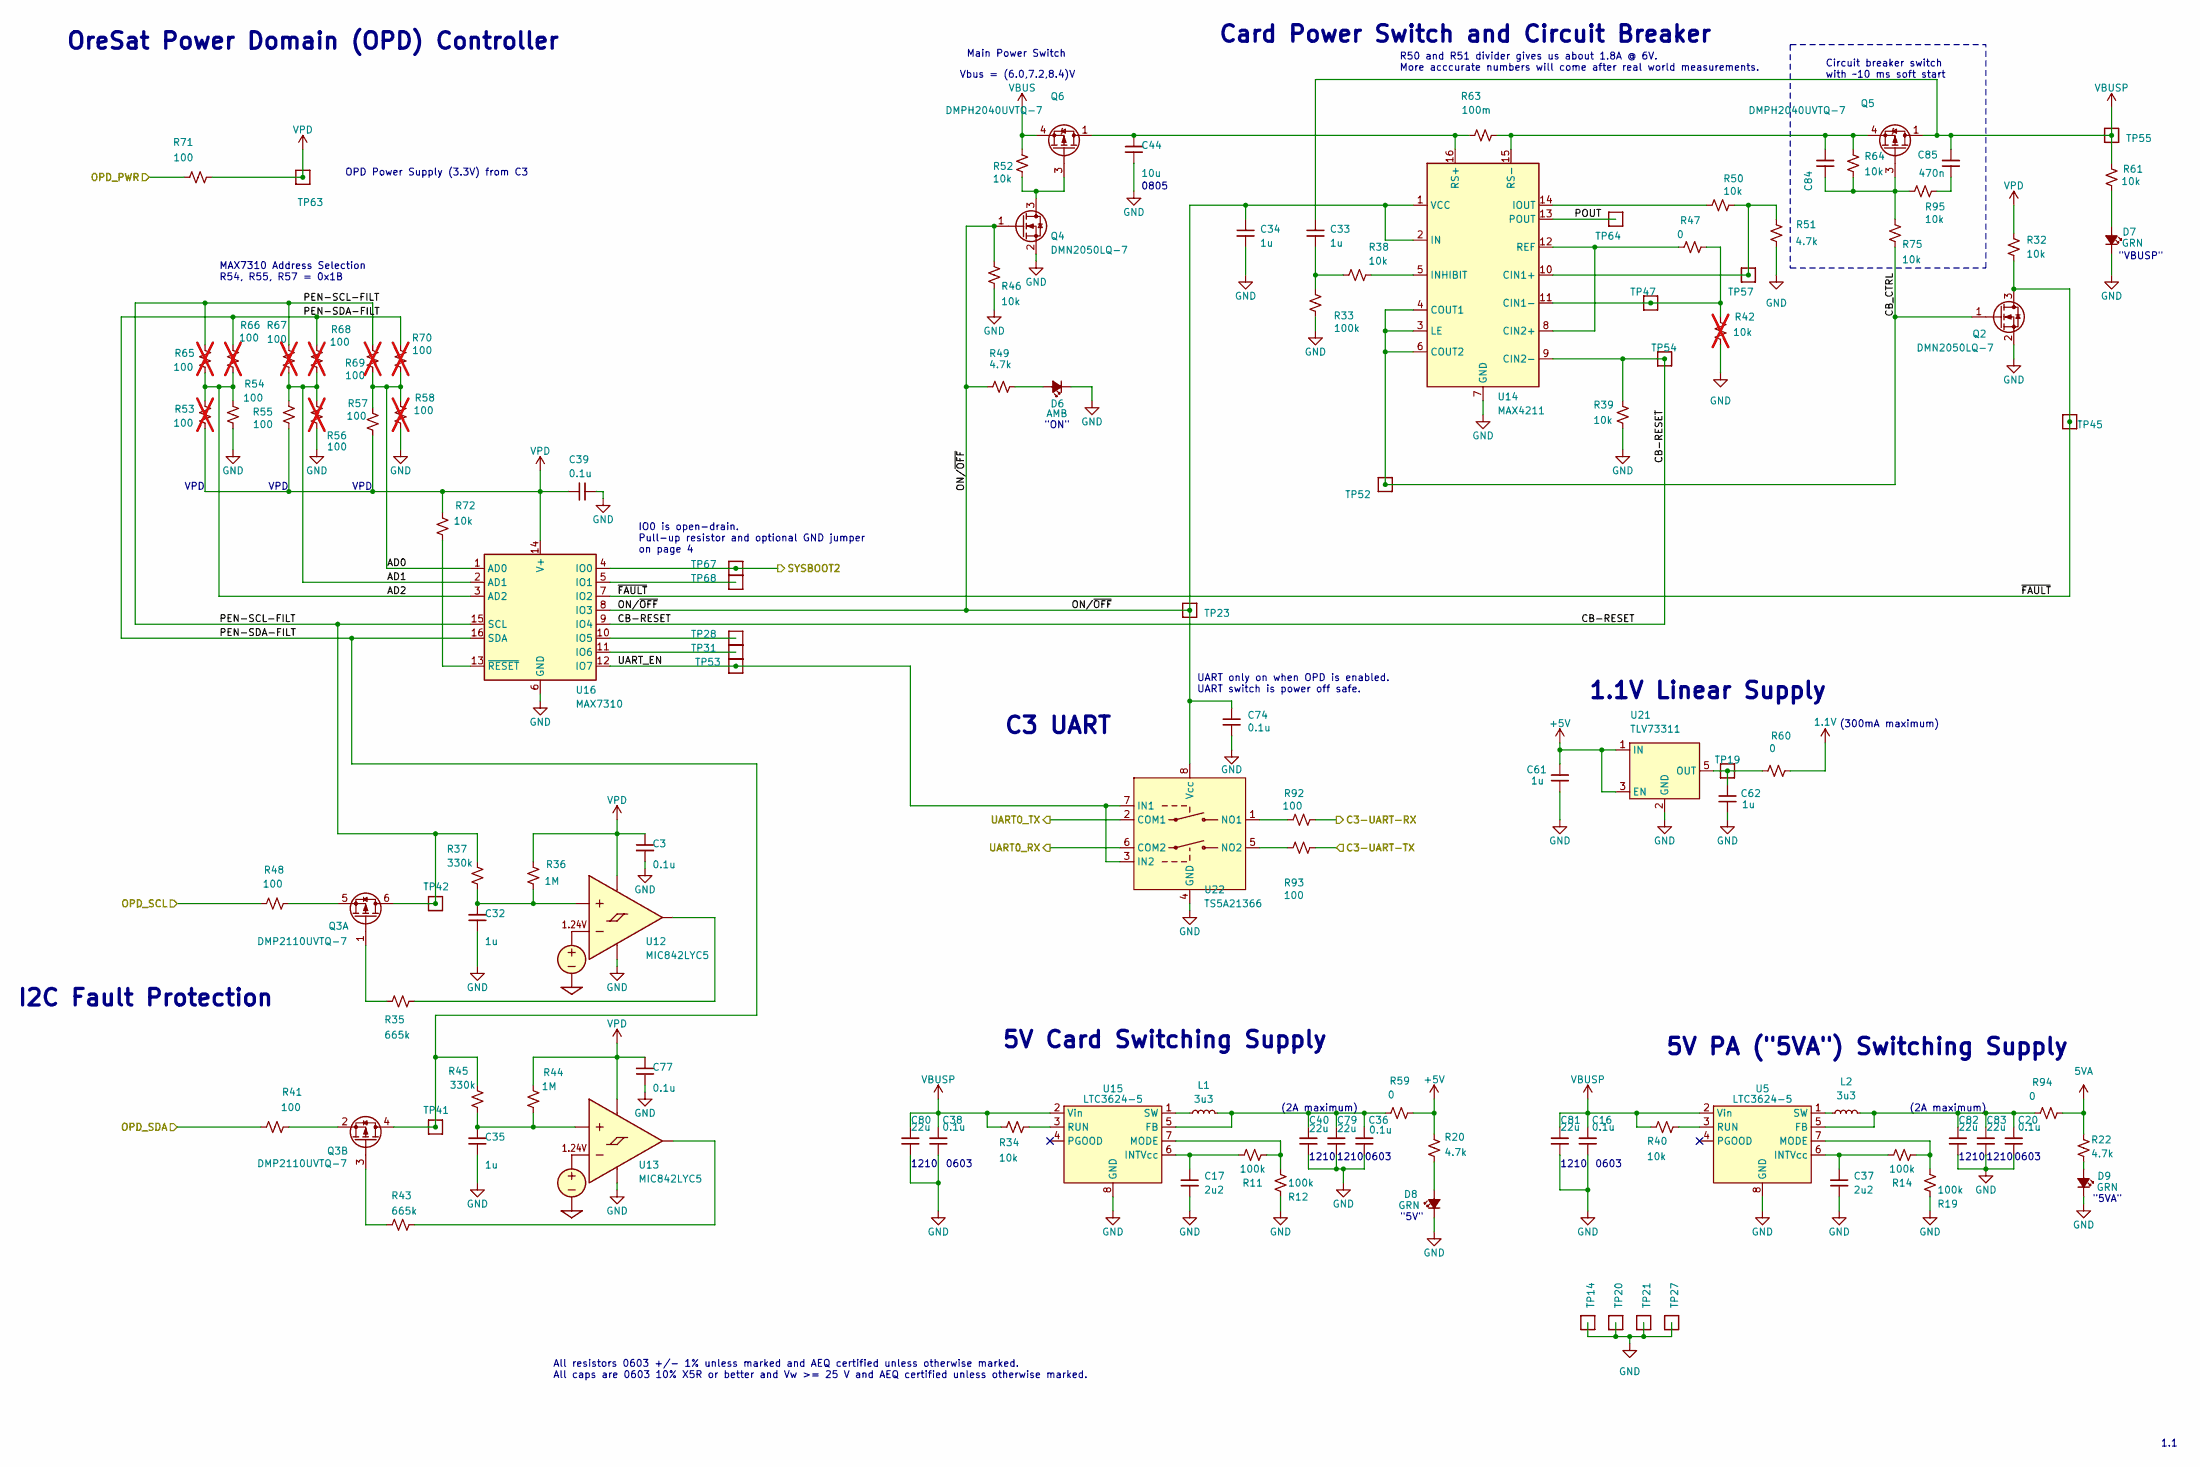
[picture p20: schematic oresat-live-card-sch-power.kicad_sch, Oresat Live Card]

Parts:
C3, C16, C20, C36, C38, C39, C74, C77: 0.1u; 0603-C-NOSILK; MPN C0603C104K5RACAUTO
C17, C37: 2u2; 0603-C-NOSILK; MPN GRT188C71E225KE13D
C32, C35: 1u; 0805-C-NOSILK; MPN GCM21BR71H105KA03L
C33, C34, C61, C62: 1u; 0603-C-NOSILK; MPN GRT188R71E105KE13D
C40, C79, C80, C81, C82, C83: 22u; C_1210_3225Metric; MPN TMK325B7226KMHP
C44: 10u; 0805-C-NOSILK; MPN GRT21BC71E106KE13K
C84: 10n; 0603-C-NOSILK; MPN C0603C103J5RACAUTO
C85: 470n; 0603-C-NOSILK; MPN C0603C474K3RACAUTO
D6: AMB; LED-0603; MPN 150060AS75000
D7, D8, D9: GRN; LED-0603; MPN 150060GS75000
L1, L2: 3u3; L_Coilcraft_XxL4020; MPN XGL4020-332MEC
Q2, Q4: DMN2050LQ-7; SOT-23; MPN DMN2050LQ-7
Q3: DMP2110UVTQ-7; SOT-23-6; MPN DMP2110UVTQ-7
Q5, Q6: DMPH2040UVTQ-7; TSOT-23-6; MPN DMPH2040UVTQ-7
R11, R12, R14, R19, R33: 100k; 0603-C-NOSILK; MPN RMCF0603FT100K
R20, R22, R49, R51: 4.7k; 0603-C-NOSILK; MPN RMCF0603FT4K70
R32, R34, R38, R39, R40, R46, R50, R52, R61, R64, R72, R75, R95: 10k; 0603-C-NOSILK; MPN RMCF0603FT10K0
R35, R43: 665k; 0603-C-NOSILK; MPN RMCF0603FT665K
R36, R44: 1M; 0603-C-NOSILK; MPN RMCF0603FT1M00
R37, R45: 330k; 0603-C-NOSILK; MPN RMCF0603FT330K
R41, R48, R54, R55, R57, R71, R92, R93: 100; 0603-C-NOSILK; MPN RMCF0603FT100R
R42: 10k; R_0603_1608Metric; MPN ERJ-3EKF1002V; not fitted
R47, R59, R60, R94: 0; 0603-C-NOSILK; MPN RMCF0603ZT0R00
R53, R56, R58, R65, R66, R67, R68, R69, R70: 100; 0603-C-NOSILK; MPN ERJ-3EKF1000V; not fitted
R63: 100m; 1206-C; MPN CSR1206FKR100
TP14, TP20, TP21, TP27, TP55: TEST-POINT; TestPoint-0.75mm-th
TP19, TP23, TP28, TP31, TP41, TP42, TP45, TP47, TP52, TP53, TP54, TP57, TP63, TP64, TP67, TP68: TEST-POINT; TestPoint_Pad_D1.0mm
U5, U15: LTC3624-5; DFN-8-1EP_3x3mm_P0.5mm_EP1.65x2.38mm_ThermalVias0.3mm; MPN LTC3624IDD-5#PBF
U12, U13: MIC842LYC5; SOT-353_SC-70-5; MPN MIC842LYC5-TR
U14: MAX4211; QFN-16-1EP_4x4mm_P0.65mm_EP2.1x2.1mm; MPN MAX4211FETE+
U16: MAX7310; QFN-16-1EP_4x4mm_P0.65mm_EP2.1x2.1mm; MPN MAX7310ATE+
U21: TLV73311; SOT-23-5; MPN TLV73311PDBVR
U22: TS5A21366; VSSOP-8_2.3x2mm_P0.5mm; MPN TS5A21366DCUR

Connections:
1.1V: R60.2; also elsewhere on the board
5VA: R22.1, R94.2; also elsewhere on the board
+5V: C61.1, R20.1, R59.2, U21.1 (IN), U21.3 (EN); also elsewhere on the board
/C3-UART-RX: R92.1; also elsewhere on the board
/C3-UART-TX: R93.1; also elsewhere on the board
/OPD_PWR: R71.1; also elsewhere on the board
/OPD_SCL: R48.1; also elsewhere on the board
/OPD_SDA: R41.1; also elsewhere on the board
/Power + OPD/AD0: R57.1, R58.2, R69.2, R70.1, U16.1 (AD0)
/Power + OPD/AD1: R55.1, R56.2, R67.2, R68.1, U16.2 (AD1)
/Power + OPD/AD2: R53.1, R54.2, R65.2, R66.1, U16.3 (AD2)
/Power + OPD/CB-RESET: R39.2, TP54.1 (1_1), U14.9 (CIN2-), U16.9 (IO4)
/Power + OPD/CB_CTRL: Q2.1 (G), R75.1, TP52.1 (1_1), U14.3 (LE), U14.4 (COUT1), U14.6 (COUT2)
/Power + OPD/ON/~OFF: C34.1, C74.1, Q4.1 (G), R46.2, R49.2, TP23.1 (1_1), U14.1 (VCC), U14.2 (IN), U16.8 (IO3), U22.8 (Vcc)
/Power + OPD/PEN-SCL-FILT: Q3.6 (D), R37.2, R65.1, R67.1, R69.1, TP42.1 (1_1), U16.15 (SCL)
/Power + OPD/PEN-SDA-FILT: Q3.4 (D), R45.2, R66.2, R68.2, R70.2, TP41.1 (1_1), U16.16 (SDA)
/Power + OPD/POUT: TP64.1 (1_1), U14.13 (POUT)
/Power + OPD/SYSBOOT2: TP67.1 (1_1), U16.4 (IO0); also elsewhere on the board
/Power + OPD/UART_EN: TP53.1 (1_1), U16.12 (IO7), U22.3 (IN2), U22.7 (IN1)
/Power + OPD/~FAULT: Q2.3 (D), R32.1, TP45.1 (1_1), U16.7 (IO2)
/UART0_RX: U22.6 (COM2); also elsewhere on the board
/UART0_TX: U22.2 (COM1); also elsewhere on the board
GND: C3.2, C16.2, C17.2, C20.2, C32.2, C34.2, C35.2, C36.2, C37.2, C38.2, C39.1, C40.2, C44.2, C61.2, C62.2, C74.2, C77.2, C79.2, C80.2, C81.2, C82.2, C83.2, D6.1 (K), D7.1 (K), D8.1 (K), D9.1 (K), Q2.2 (S), Q4.2 (S), R12.2, R19.2, R33.1, R39.1, R42.1, R46.1, R51.1, R54.1, R56.1, R58.1, TP14.1 (1_1), TP20.1 (1_1), TP21.1 (1_1), TP27.1 (1_1), U5.8 (GND), U5.9 (GND), U12.2 (GND), U13.2 (GND), U14.7 (GND), U14.17 (GND), U15.8 (GND), U15.9 (GND), U16.6 (GND), U16.17 (GND), U21.2 (GND), U22.4 (GND); also elsewhere on the board
unnamed: C33.1, R33.2, R38.2
unnamed: C85.2, R95.1
unnamed: D6.2 (A), R49.1
unnamed: D7.2 (A), R61.1
unnamed: D8.2 (A), R20.2
unnamed: D9.2 (A), R22.2
unnamed: Q3.1 (G), R35.2
unnamed: Q3.5 (S), R48.2
unnamed: Q3.3 (G), R43.2
unnamed: Q3.2 (S), R41.2
unnamed: Q4.3 (D), Q6.3 (G), R52.1
unnamed: C84.1, Q5.3 (G), R64.1, R75.2, R95.2
unnamed: C84.2, Q5.4 (S), R63.2, R64.2, U14.15 (RS-)
unnamed: C20.1, C82.1, C83.1, L2.2, R94.1, U5.5 (FB)
unnamed: C37.1, R14.1, U5.6 (INTVcc)
unnamed: R14.2, R19.1, U5.7 (MODE)
unnamed: R40.1, U5.3 (RUN)
unnamed: L2.1, U5.1 (SW)
unnamed: C32.1, R36.1, R37.1, U12.1 (INP)
unnamed: R35.1, U12.4 (OUT)
unnamed: C35.1, R44.1, R45.1, U13.1 (INP)
unnamed: R43.1, U13.4 (OUT)
unnamed: R50.2, R51.2, TP57.1 (1_1), U14.10 (CIN1+)
unnamed: R42.2, R47.1, TP47.1 (1_1), U14.11 (CIN1-)
unnamed: R47.2, U14.8 (CIN2+), U14.12 (REF)
unnamed: R38.1, U14.5 (INHIBIT)
unnamed: R50.1, U14.14 (IOUT)
unnamed: C44.1, Q6.1 (D), Q6.2 (D), Q6.5 (D), Q6.6 (D), R63.1, U14.16 (RS+)
unnamed: C36.1, C40.1, C79.1, L1.2, R59.1, U15.5 (FB)
unnamed: C17.1, R11.1, U15.6 (INTVcc)
unnamed: R11.2, R12.1, U15.7 (MODE)
unnamed: R34.1, U15.3 (RUN)
unnamed: L1.1, U15.1 (SW)
unnamed: TP68.1 (1_1), U16.5 (IO1)
unnamed: TP28.1 (1_1), U16.10 (IO5)
unnamed: TP31.1 (1_1), U16.11 (IO6)
unnamed: R72.1, U16.13 (~RESET)
unnamed: C62.1, R60.1, TP19.1 (1_1), U21.5 (OUT)
unnamed: R92.2, U22.1 (NO1)
unnamed: R93.2, U22.5 (NO2)
VBUS: Q6.4 (S), R52.2; also elsewhere on the board
VBUSP: C16.1, C33.2, C38.1, C80.1, C81.1, C85.1, Q5.1 (D), Q5.2 (D), Q5.5 (D), Q5.6 (D), R34.2, R40.2, R61.2, TP55.1 (1_1), U5.2 (Vin), U15.2 (Vin)
VPD: C3.1, C39.2, C77.1, R32.2, R36.2, R44.2, R53.2, R55.2, R57.2, R71.2, R72.2, TP63.1 (1_1), U12.5 (VDD), U13.5 (VDD), U16.14 (V+)

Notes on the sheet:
1.1V Linear Supply
"5VA"
(300mA maximum)
(2A maximum)
1210
"VBUSP"
Circuit breaker switch with ~10 ms soft start
VPD
R50 and R51 divider gives us about 1.8A @ 6V. More acccurate numbers will come after real world measurements.
I2C Fault Protection
0603
5V PA ("5VA") Switching Supply
C3 UART
All resistors 0603 +/- 1% unless marked and AEQ certified unless otherwise marked. All caps are 0603 10% X5R or better and Vw >= 25 V and AEQ certified unless otherwise marked.
UART only on when OPD is enabled. UART switch is power off safe.
0805
1.1
Card Power Switch and Circuit Breaker
MAX7310 Address Selection R54, R55, R57 = 0x1B
"5V"
OPD Power Supply (3.3V) from C3
IO0 is open-drain. Pull-up resistor and optional GND jumper on page 4
Vbus = (6.0,7.2,8.4)V
OreSat Power Domain (OPD) Controller
5V Card Switching Supply
Main Power Switch
"ON"

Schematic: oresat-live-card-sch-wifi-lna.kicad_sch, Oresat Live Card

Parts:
C90, C91, C93: 15p; 0402-C-NOSILK; MPN GJM1555C1H150JB01D
C92: 1u; 0603-C-NOSILK; MPN GRT188R71E105KE13D
C106, C111: 100n; 0603-C-NOSILK; MPN CGA3E2X7R1E104K080AA
C107, C114: 100p; 0402-C-NOSILK; MPN GCM1555C1H101GA16D
C108, C109: 1n; 0402-C-NOSILK; MPN CGA2B2NP01H102J050BA
C110: 1p; 0402-C-NOSILK; MPN GCM1555C1H1R0CA16J
C112, C113: 100n; 0402-C-NOSILK; MPN CGA2B3X7R1E104K050BB
D15: GRN; LED-0603; MPN 150060GS75000
FL1, FL2: QPQ1907SR; MPN QPQ1907SR
L3: 18n; 0603-C-NOSILK; MPN 0603DC-18NXJRW
L4: 1.5n; 0402-C-NOSILK; MPN 0402HM-1N5EKTS
R85: 4.7k; 0603-C-NOSILK; MPN RMCF0603FT4K70
R88: 10k; 0603-C-NOSILK; MPN RMCF0603FT10K0
R105: 33k; 0603-C-NOSILK; MPN RMCF0603FT33K0
R106: 0; 0402-C-NOSILK; MPN ERJ-2GE0R00X
R109: 56; 0603-C-NOSILK; MPN ERJ-3EKF56R0V
R118, R119, R120: 4.99k; 0603-C-NOSILK; MPN ERJ-3EKF4991V
R121: 100; 0603-C-NOSILK; MPN RMCF0603FT100R
TP26: TEST-POINT3X4; TestPoint-0.75mm-th
U18: TQP3M9037; DFN-8-1EP_2x2mm_P0.5mm_EP0.8x1.6mm; MPN TQP3M9037
U27: PAT1220-C-3DB; RF_Attenuator_Susumu_PAT1220; MPN PAT1220-C-3DB-T5
U28: PD2328J5050S2HF; MPN PD2328J5050S2HF
U29: LTC5538; DFN-8-1EP_3x3mm_P0.5mm_EP1.65x2.38mm; MPN LT5538IDD#TRPBF

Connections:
5VA: C106.2, C107.1, C112.2, C113.2, C114.1, R106.2, R118.1, U29.5 (VCC); also elsewhere on the board
/SIP B: ADC + Crystals/RF/RX_IN_DETECTED: C111.1, R119.2, R120.2, TP26.1 (1_1); also elsewhere on the board
/WiFi LNA/AR9271_RX: R121.1, U28.4 (OUTPUT1); also elsewhere on the board
/WiFi LNA/LNA_SHUTDOWN: R85.1, R105.1; also elsewhere on the board
/WiFi LNA/RX_FROM_SWITCH: FL1.1 (INPUT); also elsewhere on the board
GND: C91.2, C92.2, C106.1, C107.2, C108.2, C110.1, C111.2, C114.2, D15.1 (K), FL1.2 (GND), FL1.3 (GND), FL1.5 (GND), FL2.2 (GND), FL2.3 (GND), FL2.5 (GND), R88.2, R109.2, R120.1, U18.9 (GND), U27.3, U28.1 (GND), U28.3 (GND), U28.5 (GND), U29.4 (GND), U29.9 (GND); also elsewhere on the board
unnamed: C91.1, C92.1, L3.1, R106.1
unnamed: C93.2, U27.1
unnamed: C109.1, L4.2, R109.1
unnamed: D15.2 (A), R85.2
unnamed: C90.1, FL1.4 (OUTPUT)
unnamed: FL2.1 (INPUT), U27.2
unnamed: FL2.4 (OUTPUT), U28.2 (INPUT)
unnamed: C90.2, U18.2 (RF_IN)
unnamed: C93.1, L3.2, U18.7 (RF_OUT)
unnamed: R88.1, R105.2, U18.6 (SHUT_DOWN)
unnamed: C110.2, L4.1, R121.2, U28.6 (OUTPUT2)
unnamed: C113.1, U29.7 (CAP+)
unnamed: C112.1, U29.6 (CAP-)
unnamed: R118.2, U29.1 (EN)
unnamed: C109.2, U29.2 (IN+)
unnamed: C108.1, U29.3 (IN-)
unnamed: R119.1, U29.8 (OUT)

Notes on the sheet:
~ 1.65 V max which is < 1.8 V of Octavo ADC max
0402
Changed from 100 to 56
~ 3 V max
RF Detector, transforms RF detected into a DC sense line for Octavo to read
All resistors 0603 +/- 1% unless marked and AEQ certified unless otherwise marked. All caps are 0603 10% X5R or better and Vw >= 25 V and AEQ certified unless otherwise marked.
"LNA OFF"

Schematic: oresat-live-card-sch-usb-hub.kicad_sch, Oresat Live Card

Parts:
C1, C27, C28, C42, C54, C55, C56, C57, C58, C59, C60, C65, C66, C67, C68, C70, C71, C72: 0.1u; 0603-C-NOSILK; MPN C0603C104K5RACAUTO
C53, C69, C76, C96, C97: 10u; 0805-C-NOSILK; MPN GRT21BC71E106KE13K
C63, C64: 12p; 0603-C-NOSILK; MPN KAM15ACG2A120KT
C73: 1u; 0603-C-NOSILK; MPN GRT188R71E105KE13D
D10: GRN; LED-0603; MPN 150060GS75000
FB1, FB3: BLM18KG300TH1D; 0603; MPN BLM18KG300JH1D
FB4, FB5: MMZ1608Y221BTD25; 0603; MPN MMZ1608Y221BTD25
R6, R7, R21, R76, R77, R79, R89, R90, R91: 10k; 0603-C-NOSILK; MPN RMCF0603FT10K0
R29: 4.7k; 0603-C-NOSILK; MPN RMCF0603FT4K70
R78: 9.53k; 0603-C-NOSILK; MPN ERJ-3EKF9531V
R83: 90.9k; 0603-C-NOSILK; MPN RMCF0603FT90K9
R98, R99: 0; 0603-C-NOSILK; MPN RMCF0603ZT0R00
TP1, TP15: TEST-POINT; TestPoint_Pad_D1.0mm
TP13, TP16, TP17, TP18: TEST-POINT3X4; TestPoint_Pad_D1.0mm
U2: TUSB4020BI; TQFP-48-1EP_7x7mm_P0.5mm_EP5x5mm; MPN TUSB4020BIPHPRQ1
U9, U20: TPS2041BQDBVRQ1; DBV5; MPN TPS2041BQDBVRQ1
Y3: 24MHz; 5X3.2-4SMD; MPN ECS-240-12-30BQ-AEN-TR

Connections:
1.1V: FB4.2; also elsewhere on the board
+3.3V: FB5.2, R6.2, R7.2, R77.1, R79.2, R90.2, R91.2; also elsewhere on the board
+5V: R98.2, R99.2; also elsewhere on the board
/SIP B: ADC + Crystals/UP_N: U2.27 (USB_DM_UP); also elsewhere on the board
/SIP B: ADC + Crystals/UP_P: U2.26 (USB_DP_UP); also elsewhere on the board
/SIP B: ADC + Crystals/USB_VBUS: R83.1; also elsewhere on the board
/SIP C: SD + eMMC + CAN/GRSTz: R89.2, U2.11 (GRSTz); also elsewhere on the board
/USB HUB/CAMERA_USB_N: U2.42 (USB_DM_DN1); also elsewhere on the board
/USB HUB/CAMERA_USB_P: U2.41 (USB_DP_DN1); also elsewhere on the board
/USB HUB/CAMERA_VUSB: FB3.2, TP1.1 (1_1); also elsewhere on the board
/USB HUB/WIFI_ENABLE: R29.1; also elsewhere on the board
/USB HUB/WIFI_STATUS: D10.1 (K); also elsewhere on the board
/USB HUB/WIFI_USB_N: U2.15 (USB_DM_DN2); also elsewhere on the board
/USB HUB/WIFI_USB_P: U2.14 (USB_DP_DN2); also elsewhere on the board
/USB HUB/WIFI_VUSB: FB1.2, R21.1, R29.2, TP15.1 (1_1); also elsewhere on the board
GND: C1.2, C27.2, C28.2, C42.2, C53.2, C54.2, C55.2, C56.2, C57.2, C58.2, C59.2, C60.2, C63.2, C64.2, C65.2, C66.2, C67.2, C68.2, C69.2, C70.2, C71.2, C72.2, C73.2, C76.2, C96.2, C97.2, R76.1, R78.2, R89.1, U2.10 (TEST), U2.49 (GND), U9.2 (GND), U20.2 (GND), Y3.2 (G), Y3.4 (G); also elsewhere on the board
unnamed: C54.1, C55.1, C57.1, C59.1, C65.1, C67.1, C69.1, FB4.1, U2.1 (VDD), U2.12 (VDD), U2.18 (VDD), U2.30 (VDD), U2.34 (VDD), U2.45 (VDD)
unnamed: D10.2 (A), R21.2
unnamed: TP13.1 (1_1), U2.36 (FULLPWRMGMTz/SMBA1)
unnamed: R79.1, U2.35 (GANGED/SMBA2/HS_UP)
unnamed: R91.1, U2.5 (OVERCUR1z), U20.3 (~OC)
unnamed: R6.1, U2.8 (OVERCUR2z), U9.3 (~OC)
unnamed: R90.1, U2.4 (PWRCTL1/BATEN1), U20.4 (~EN)
unnamed: R7.1, U2.6 (PWRCTL2/BATEN2), U9.4 (~EN)
unnamed: R77.2, U2.21 (PWRCTL_POL)
unnamed: TP17.1 (1_1), U2.2 (SCL/SMBCLK)
unnamed: TP16.1 (1_1), U2.3 (SDA/SMBDAT)
unnamed: TP18.1 (1_1), U2.22 (SMBUSz)
unnamed: R78.1, U2.24 (USB_R1)
unnamed: R76.2, R83.2, U2.9 (USB_VBUS)
unnamed: C63.1, U2.38 (XI), Y3.1
unnamed: C64.1, U2.39 (XO), Y3.3
unnamed: C1.1, R98.1, U9.5 (IN)
unnamed: C27.1, C53.1, C96.1, FB3.1, U9.1 (OUT)
unnamed: C28.1, R99.1, U20.5 (IN)
unnamed: C42.1, C76.1, C97.1, FB1.1, U20.1 (OUT)
VDD33: C56.1, C58.1, C60.1, C66.1, C68.1, C70.1, C71.1, C72.1, C73.1, FB5.1, U2.7 (VDD33), U2.13 (VDD33), U2.23 (VDD33), U2.25 (VDD33), U2.33 (VDD33), U2.37 (VDD33), U2.40 (VDD33), U2.48 (VDD33)

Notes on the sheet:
Wifi USB
Ordering of ferrite bead and capacitor taken from TPS2041 datasheet (see figure 9-13)
Assert GRSTz via GPIO to deactivate USB hub and clear registers
Camera USB
"WIFI"
All resistors 0603 +/- 1% unless marked and AEQ certified unless otherwise marked. All caps are 0603 10% X5R or better and Vw >= 25 V and AEQ certified unless otherwise marked.

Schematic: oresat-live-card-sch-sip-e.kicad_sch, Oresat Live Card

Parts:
U7: OSD3358-512M-BSM; U-Octavo-OSD335X-BGA-256; MPN OSD3358-512M-BSM

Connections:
GND: U7.D8 (DGND@1), U7.D9 (DGND@2), U7.E5 (DGND@3), U7.E6 (DGND@4), U7.E7 (DGND@5), U7.E8 (DGND@6), U7.E9 (DGND@7), U7.E10 (DGND@8), U7.E11 (DGND@9), U7.E12 (DGND@10), U7.F5 (DGND@11), U7.F12 (DGND@12), U7.G5 (DGND@13), U7.G12 (DGND@14), U7.H4 (DGND@15), U7.H5 (DGND@16), U7.H12 (DGND@17), U7.H13 (DGND@18), U7.J4 (DGND@19), U7.J5 (DGND@20), U7.J12 (DGND@21), U7.J13 (DGND@22), U7.K5 (DGND@23), U7.K12 (DGND@24), U7.L5 (DGND@25), U7.L12 (DGND@26), U7.M5 (DGND@27), U7.M6 (DGND@28), U7.M7 (DGND@29), U7.M8 (DGND@30), U7.M9 (DGND@31), U7.M10 (DGND@32), U7.M11 (DGND@33), U7.M12 (DGND@34), U7.N8 (DGND@35), U7.N9 (DGND@36); also elsewhere on the board

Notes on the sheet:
All resistors 0603 +/- 1% unless marked and AEQ certified unless otherwise marked. All caps are 0603 10% X5R or better and Vw >= 25 V and AEQ certified unless otherwise marked.

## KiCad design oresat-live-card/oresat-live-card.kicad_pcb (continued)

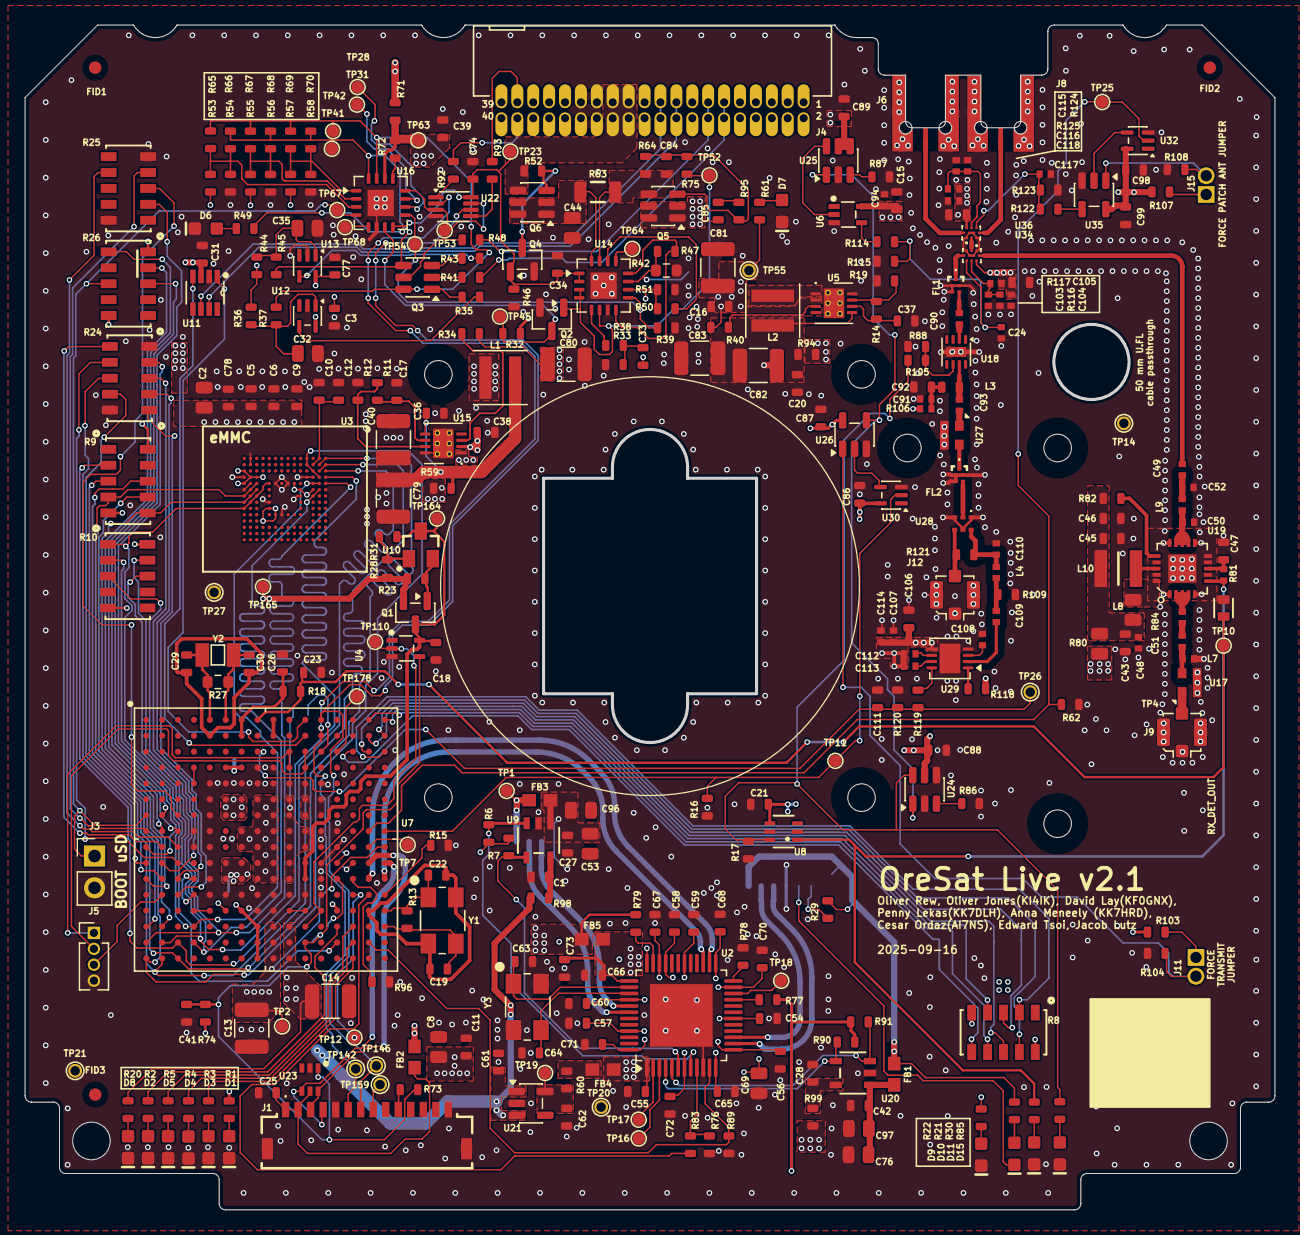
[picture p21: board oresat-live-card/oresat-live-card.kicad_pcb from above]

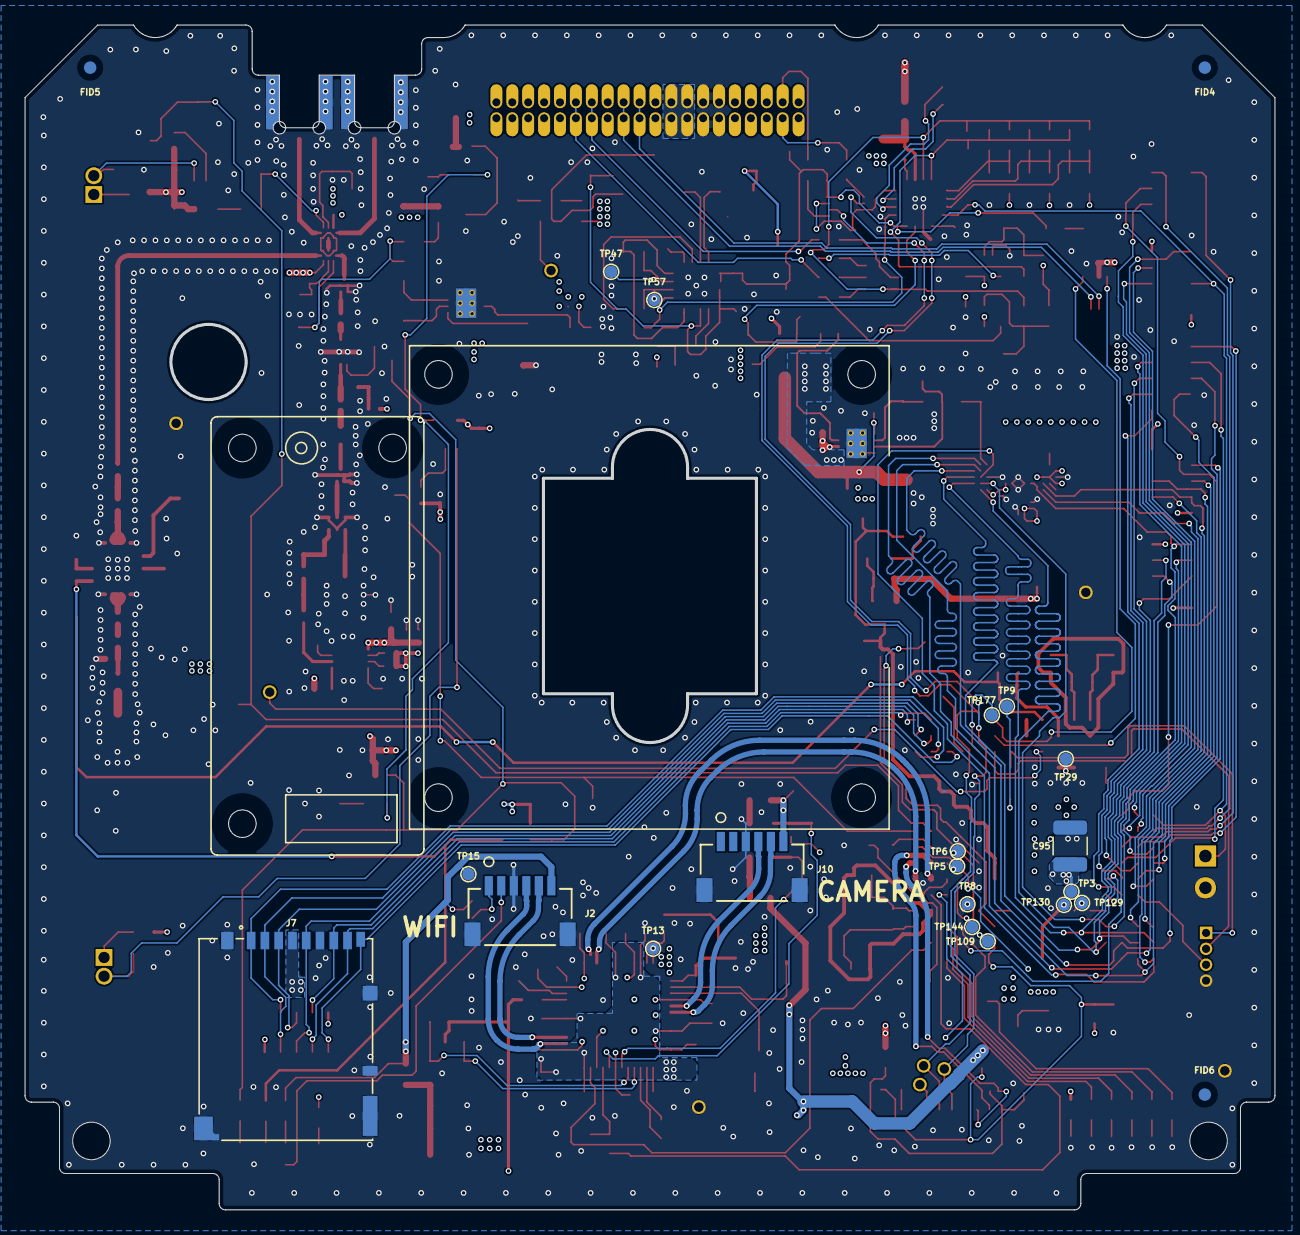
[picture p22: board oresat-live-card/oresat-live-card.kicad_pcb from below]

Board: 4 copper layers, 99.8 x 94.6 mm, 373 parts (23 on the bottom side), 247 nets.

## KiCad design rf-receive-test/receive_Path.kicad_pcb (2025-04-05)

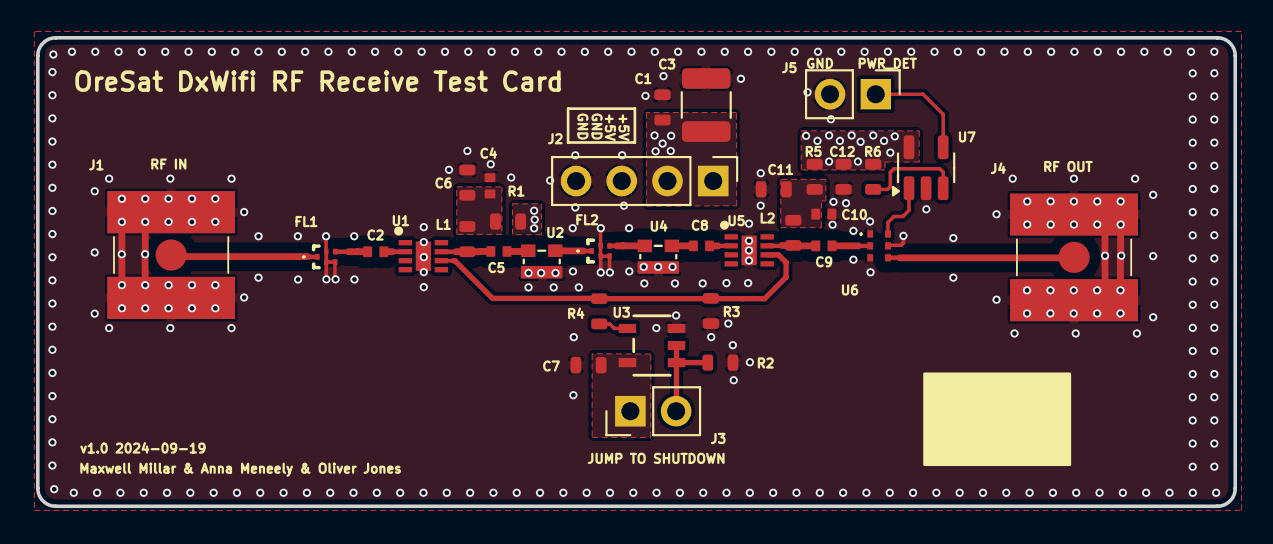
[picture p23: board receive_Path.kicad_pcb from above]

Board: 4 copper layers, 66.5 x 26.0 mm, 34 parts (0 on the bottom side), 22 nets.

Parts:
C1: 2u2; 0603-C-NOSILK
C2, C4, C5, C8, C9, C10: 15p; 0402-C-NOSILK
C3: 22u; C_1210_3225Metric
C6, C11: 1u; 0603-C-NOSILK
C7, C12: 100n; 0603-C-NOSILK
FL1, FL2: QPQ1907SR
J1: 142-0711-201; SMA 142-0711-201
J2: 0022232041; PinHeader_1x04_P2.54mm_Vertical
J3, J5: 0022232021; PinHeader_1x02_P2.54mm_Vertical
J4: Conn_Coaxial_142-0711-201; SMA 142-0711-201
L1, L2: 18nH; 0603-C-NOSILK
R1, R5: 0; 0603-C-NOSILK
R2, R4: 10k; 0603-C-NOSILK
R3: 33K; 0603-C-NOSILK
R6: 10K; 0603-C-NOSILK
U1, U5: TQP3M9037
U2, U4: PAT1220-C-3DB; PAT1220(0805)
U3: SN74LVC1G32QDBVRQ1; DBV5 SN74LVC1G3T2Q
U6: PD2328J5050S2HF
U7: LTC5505-1ES5; TSOT-23-5

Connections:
5VA: C1.1, C3.1, C7.1, C12.1, J2.1, J2.2, J3.1, R1.2, R5.2, R6.2, U3.5 (VCC), U7.5 (VCC)
/PWR_DET_IN: U6.6 (OUTPUT2), U7.1 (RFIN)
/PWR_DET_OUT: J5.1, U7.4 (VOUT)
/RF_ATTEN1_OUT1: FL2.1 (INPUT), U2.2
/RF_ATTEN2_OUT1: C8.1, U4.2
/RF_ATTEN2_OUT2: C8.2, U5.2 (RF_IN)
/RF_BPF2_OUT: FL2.4 (OUTPUT), U4.1
/RF_BPF_OUT1: C2.1, FL1.4 (OUTPUT)
/RF_BPF_OUT2: C2.2, U1.2 (RF_IN)
/RF_IN: FL1.1 (INPUT), J1.3
/RF_LNA1_OUT1: C5.1, L1.2, U1.7 (RF_OUT)
/RF_LNA1_OUT2: C5.2, U2.1
/RF_LNA2_OUT1: C9.1, L2.2, U5.7 (RF_OUT)
/RF_LNA2_OUT2: C9.2, U6.2 (INPUT)
/RF_OUT1: J4.3, U6.4 (OUTPUT1)
GND: C1.2, C3.2, C4.2, C6.2, C7.2, C10.2, C11.2, C12.2, FL1.2 (GND), FL1.3 (GND), FL1.5 (GND), FL2.2 (GND), FL2.3 (GND), FL2.5 (GND), J1.1 (In), J1.2 (Ext), J2.3, J2.4, J4.1 (In), J4.2 (Ext), J5.2, R2.1, R3.1, U1.9 (GND), U2.3, U3.3 (GND), U4.3, U5.9 (GND), U6.1 (GND), U6.3 (GND), U6.5 (GND), U7.2 (GND)
unnamed: C4.1, C6.1, L1.1, R1.1
unnamed: C10.1, C11.1, L2.1, R5.1
unnamed: J3.2, R2.2, U3.1 (A), U3.2 (B)
unnamed: R3.2, R4.1, U1.6 (SHUT_DOWN), U5.6 (SHUT_DOWN)
unnamed: R4.2, U3.4 (Y)
unnamed: R6.1, U7.3 (~SHDN)

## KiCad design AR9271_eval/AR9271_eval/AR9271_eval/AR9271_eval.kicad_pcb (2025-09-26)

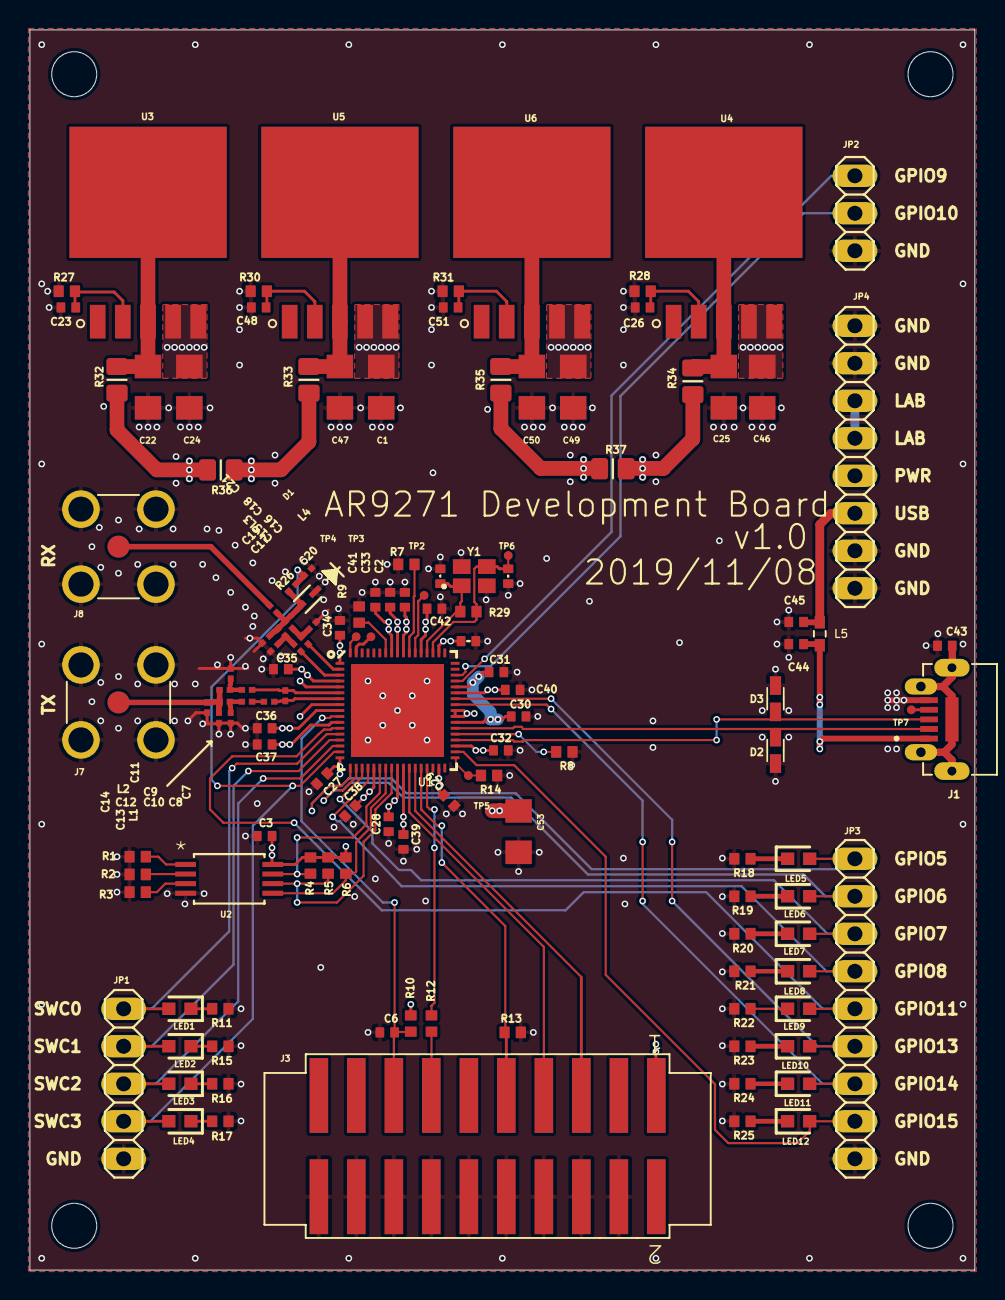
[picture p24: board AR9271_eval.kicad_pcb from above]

Board: 4 copper layers, 64.0 x 84.0 mm, 135 parts (0 on the bottom side), 80 nets.

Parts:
C1, C22, C24, C25, C46, C47, C49, C50, C53: 4.7uF; C1206_334
C2, C3, C6, C26, C27, C28, C29, C30, C31, C32, C33, C34, C43, C45, C51: 100n; .0402-B-NOSILK
C4, C5, C35, C36: 10p; .0402-B-NOSILK
C7: 2.2pF; .0201-B-NOSILK
C8, C9, C15, C16, C20: 10.0pF; .0201-B-NOSILK
C10, C11, C12, C13: 2.0pF; .0201-B-NOSILK
C14, C19: 1.0pF; .0201-B-NOSILK
C17, C18: 1.5pF; .0201-B-NOSILK
C21: 100.0pF; .0201-B-NOSILK
C23, C48: 10nF; .0402-B-NOSILK
C37: 100p; .0402-B-NOSILK
C38, C40: 1n; .0402-B-NOSILK
C39, C44: 10n; .0402-B-NOSILK
C41, C42, C52: 1u; .0402-B-NOSILK
D1: SMP1321-079LF; SOD523
D2, D3: PGB1010603MR; ESD_PGB1010603MR
H1, H2, H3, H4: STAND-OFFTIGHT; STAND-OFF-TIGHT_519
J1: UJ2-MIBH2-4-SMT-TR; CUI_UJ2-MIBH2-4-SMT-TR
J3: HTST-110-01-XX-DV
J7, J8: 132134-15; AMPHENOL_132134-15
JP1: 1X05_325
JP2: 1X03_325
JP3: 1X09_325
JP4: 1X08_325
L1, L2: 1.8nH; .0201-B-NOSILK
L3, L4: 2.2nH; .0201-B-NOSILK
L5: BLM18PG221SH1D; INDC1608X95
LED1, LED2, LED3, LED4, LED5, LED6, LED7, LED8, LED9, LED10, LED11, LED12: LTST-C193KGKT-5A; LEDC1607X80N
R1: DNP; .0402-A-NOSILK
R2, R3: 0; .0402-A-NOSILK
R4, R7, R10, R13, R14: 10k; .0402-A-NOSILK
R5, R6: 4.7k; .0402-A-NOSILK
R8: 51.1; .0402-A-NOSILK
R9: 6.19k; .0402-A-NOSILK
R11, R15, R16, R17, R18, R19, R20, R21, R22, R23, R24, R25: 510; .0402-A-NOSILK
R12: 33; .0402-A-NOSILK
R26: 1.0k; .0201-B-NOSILK
R27, R30: 330k; .0402-A-NOSILK
R28, R31: 120k; .0402-A-NOSILK
R29: 1M; .0402-A-NOSILK
R32, R33, R34, R35: 0; .0805-B
R36, R37: DNP; .0805-B
TP2, TP3, TP4, TP5, TP6, TP7: TPTP06R; TP06R_385
U1: U-ATHEROS-AR9271; QFN-68
U2: AT24C04C-XHM-T; 8X
U3, U4, U5, U6: LT3080EQPBF; DDPAK-5_Q
Y1: ECS-400-10-36-CKY-TR; XTAL_ECS-400-10-36-CKY-TR

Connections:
1V2_A: C2.1, C41.1, C42.1, R35.2, R37.1, U1.56, U1.59, U1.61
1V2_D: C37.1, C38.1, C39.1, C40.1, R34.2, R37.2, U1.11, U1.22, U1.27, U1.42, U1.43, U1.46
3V3_A: C33.1, C34.1, C35.1, C36.1, C52.1, R33.2, R36.1, U1.1, U1.4, U1.9, U1.53, U1.60
3V3_D: C3.1, C27.1, C28.1, C29.1, C30.1, C31.1, C32.1, C53.1, J3.1, R4.2, R5.2, R6.2, R10.2, R32.2, R36.2, U1.5, U1.8, U1.17, U1.26, U1.33, U1.37, U1.41, U1.47, U2.8
A1: R2.2, U2.2
A2: R3.2, U2.3
BIASREF: R9.1, U1.62
CTRL1: R7.2, U1.58
CTRL2: TP2.TP, U1.57
EE-SCK: R5.1, U1.25, U2.6
EE-SDA: R6.1, U1.24, U2.5
EE-WP: R4.1, U1.23, U2.7
GND: C1.2, C2.2, C3.2, C4.2, C5.2, C6.2, C11.1, C13.1, C14.2, C17.2, C19.2, C20.2, C22.2, C23.2, C24.2, C25.2, C26.2, C27.2, C28.2, C29.2, C30.2, C31.2, C32.2, C33.2, C34.2, C35.2, C36.2, C37.2, C38.2, C39.2, C40.2, C41.2, C42.2, C43.2, C44.2, C45.2, C46.2, C47.2, C48.2, C49.2, C50.2, C51.2, C52.2, C53.2, D1.1, D2.2, D3.2, J1.5, J3.4, J3.6, J3.8, J3.10, J3.12, J3.14, J3.16, J3.18, J3.20, J7.P1, J7.P2, J7.P3, J7.P4, J8.P1, J8.P2, J8.P3, J8.P4, JP1.5, JP2.3, JP3.9, JP4.1, JP4.2, JP4.7, JP4.8, L1.1, L4.1, R1.1, R2.1, R3.1, R7.1, R8.1, R9.2, R11.1, R13.1, R14.1, R15.1, R16.1, R17.1, R18.1, R19.1, R20.1, R21.1, R22.1, R23.1, R24.1, R25.1, R27.1, R28.1, R30.1, R31.1, U1.69, U2.4, Y1.2, Y1.4
GPIO5: JP3.1, LED5.2, U1.18
GPIO6: JP3.2, LED6.2, U1.19
GPIO7: JP3.3, LED7.2, U1.20
GPIO8: JP3.4, LED8.2, U1.21
GPIO9: JP2.1, U1.48
GPIO10: JP2.2, U1.49
GPIO11: JP3.5, LED9.2, U1.12
GPIO13: JP3.6, LED10.2, U1.45
GPIO14: JP3.7, LED11.2, U1.44
GPIO15: JP3.8, LED12.2, U1.36
LDO_IN: C1.1, C24.1, C46.1, C49.1, JP4.5, U3.4, U3.5, U4.4, U4.5, U5.4, U5.5, U6.4, U6.5
unnamed: J1.4, TP7.TP
unnamed: JP4.3, JP4.4
unnamed: R1.2, U2.1
unnamed: LED1.1, R11.2
unnamed: LED2.1, R15.2
unnamed: C10.2, C12.1, L1.2
unnamed: C15.2, C17.1, L3.1
unnamed: C16.2, C18.1, L4.2
unnamed: C9.2, C11.2, L2.1
unnamed: LED3.1, R16.2
unnamed: LED4.1, R17.2
unnamed: LED5.1, R18.2
unnamed: C8.2, C10.1
unnamed: C23.1, R27.2, U3.2
unnamed: C18.2, C19.1, C21.1, D1.2, L3.2, R26.2
unnamed: C26.1, R28.2, U4.2
unnamed: LED6.1, R19.2
unnamed: LED7.1, R20.2
unnamed: LED8.1, R21.2
unnamed: LED9.1, R22.2
unnamed: C43.1, J1.SH1, J1.SH2, J1.SH3, J1.SH4, J1.SH5
unnamed: C22.1, R32.1, U3.3, U3.6
unnamed: LED10.1, R23.2
unnamed: LED11.1, R24.2
unnamed: LED12.1, R25.2
unnamed: C25.1, R34.1, U4.3, U4.6
unnamed: C48.1, R30.2, U5.2
unnamed: C47.1, R33.1, U5.3, U5.6
unnamed: C51.1, R31.2, U6.2
unnamed: C50.1, R35.1, U6.3, U6.6
PDET: TP4.TP, U1.68
RCV_IN: C21.2, J8.1
RFIN_N: C16.1, U1.2
RFIN_P: C15.1, U1.3
RFOUT_N: C7.1, C9.1, U1.6
RFOUT_P: C7.2, C8.1, U1.7
SPIBOOT: R14.2, TP5.TP, U1.35
SWCOM0: JP1.1, LED1.2, U1.13
SWCOM1: JP1.2, LED2.2, U1.14
SWCOM2: JP1.3, LED3.2, U1.15
SWCOM3: C20.1, JP1.4, LED4.2, R26.1, U1.16
TCK: J3.9, R13.2, U1.30
TDI: J3.5, U1.29
TDO: J3.13, R12.2
TDO-PRE-RES: R12.1, U1.31
TMS: J3.7, U1.28
TXRTUNE: R8.2, U1.39
USB+5V: C45.1, JP4.6, L5.2
USB_+V: C44.1, J1.1, L5.1
USB_DM: D2.1, J1.2, U1.40
USB_DP: D3.1, J1.3, U1.38
XMIT_OUT: C12.2, C13.2, C14.1, J7.1, L2.2
XPABIOS: TP3.TP, U1.67
XTALI: C4.1, R29.1, U1.55, Y1.1
XTALO: C5.1, R29.2, TP6.TP, U1.54, Y1.3
~RST: C6.1, J3.15, R10.1, U1.10

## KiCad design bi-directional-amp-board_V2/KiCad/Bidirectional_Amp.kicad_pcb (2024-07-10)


Board: 4 copper layers, 52.0 x 68.4 mm, 135 parts (0 on the bottom side), 53 nets.

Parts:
@HOLE0, @HOLE1, @HOLE2, @HOLE3, @HOLE4, @HOLE5, @HOLE6, @HOLE7, @HOLE8, @HOLE9, @HOLE10, @HOLE11, @HOLE12, @HOLE13, @HOLE14, @HOLE15, @HOLE16, @HOLE17, @HOLE18, @HOLE19, @HOLE20, @HOLE21, @HOLE22, @HOLE23, @HOLE24, @HOLE25, @HOLE26, @HOLE27, @HOLE28, @HOLE29: (no value)
C1, C3, C26, C28: 15p; .0402-C-NOSILK
C2, C27: 15p; .0402-B-NOSILK
C4, C29: 1uF; .0603-B-NOSILK
C5, C6, C7, C8, C10, C14, C31, C39, C41: 100n; .0402-B-NOSILK
C9, C12, C30, C33: 100p; .0402-B-NOSILK
C11, C32: DNP; .0402-B-NOSILK
C15, C16, C17: 100nF; .0402-B-NOSILK
C18: 100pF; .0402-B-NOSILK
C19: 1000pF; .0402-B-NOSILK
C20: 100pF; .0603-C-NOSILK
C21: 3.0pF; .0402-C-NOSILK
C22: 2.2pF; .0402-C-NOSILK
C23: 1.6pF; .0402-C-NOSILK
C24: 4.7pF; .0603-C-NOSILK
C34: 4.7uF; C1206_334
C35: 22uF; C1210_334
FL1, FL2: QPQ1907; FIL_B39162B9417K610
H1, H2, H3, H4: STAND-OFFTIGHT; STAND-OFF-TIGHT
J1, J2, J3, J4, J6, J7: 142-0701-851_ALT; 142-0701-851
JP1, JP3, JP4: 1X03_325
JP6: 1X04_325
L1: 1008HQ-10NXJLB1008_IMPERIAL_2520_METRIC; INDC2520X120N
L2: 6.8nH; 0805CS
L3: 1.2nH; 0402CS1N2XJLW
L4, L5: 68nH; 0603CS-68NXJLW
LED1: LTST-C193KRKT-5A; LEDC1607X80N
LED2: LTST-C193KGKT-5A; LEDC1607X80N
R1, R2: 147; .0603-C-NOSILK
R3: 17.8; .0603-C-NOSILK
R4: 294; .0603-C-NOSILK
R5, R15, R21, R24, R26, R28, R29, R31, R37: 10k; .0402-B-NOSILK
R6, R9: 17.8; .0402-C-NOSILK
R7, R8, R10, R13: 294; .0402-C-NOSILK
R11, R12: 499k; .0402-B-NOSILK
R14, R23: 0; .0603-B-NOSILK
R16, R22, R25, R27: 5.62k; .0402-B-NOSILK
R17: 0; R0805_334
R18: 1.2; R0402_334
R19: 110; .0402-B-NOSILK
R20: 220; .0603-C-NOSILK
R30: 33k; .0402-B-NOSILK
R32, R36: 1k; .0402-B-NOSILK
SW1: TL36PO; TL3XPO_380
U1, U12: SN74LVC1G32DBVR; DBV5
U2, U3: LTC6994-1; TSOT-23_S6
U4, U5: TQP3M9037; DFN8-2X2-WITH-PAD
U6, U9, U11: SN74LV1T34DBVR; SOT95P280X145-5N
U7, U8: QPC1022
U10: TQP9111; QFN50P400X400X102-21N

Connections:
+5V: C5.1, C6.1, C7.1, C8.1, C9.1, C10.1, C14.1, C30.1, C31.1, C34.1, C35.1, C39.1, C41.1, JP6.1, JP6.2, LED2.2, R5.2, R14.2, R15.1, R17.2, R23.2, R24.1, U1.5, U2.5, U3.4, U3.5, U6.5, U7.7, U8.7, U9.5, U11.5, U12.5
ANT_SEL+3.3V: JP3.1, JP3.3, R28.2, U9.2
ANT_SEL_+5.0V: R21.1, U9.4
AR9271_TX_+3.3V: JP1.1, JP1.3, R37.2, U11.2
AS-CTRL: C11.1, R21.2, R22.1, U7.5
AS-EN: C12.1, R15.2, R16.1, U7.6
GND: C2.1, C4.2, C5.2, C6.2, C7.2, C8.2, C9.2, C10.2, C11.2, C12.2, C14.2, C15.2, C16.2, C17.2, C18.2, C19.2, C21.2, C22.2, C23.2, C27.1, C29.2, C30.2, C31.2, C32.2, C33.2, C34.2, C35.2, C39.2, C41.2, FL1.2, FL1.3, FL1.5, FL2.2, FL2.3, FL2.5, J1.GND1, J1.GND2, J1.GND3, J1.GND4, J2.GND1, J2.GND2, J2.GND3, J2.GND4, J3.GND1, J3.GND2, J3.GND3, J3.GND4, J4.GND1, J4.GND2, J4.GND3, J4.GND4, J6.GND1, J6.GND2, J6.GND3, J6.GND4, J7.GND1, J7.GND2, J7.GND3, J7.GND4, JP1.2, JP3.2, JP4.2, JP6.3, JP6.4, R2.1, R4.2, R7.2, R8.2, R10.2, R11.1, R12.1, R13.2, R16.2, R22.2, R25.2, R27.2, R28.1, R29.1, R31.2, R32.1, R36.1, R37.1, SW1.1, U1.3, U2.2, U2.4, U3.2, U4.1, U4.3, U4.4, U4.5, U4.8, U4.PAD, U5.1, U5.3, U5.4, U5.5, U5.8, U5.PAD, U6.3, U7.1, U7.3, U7.9, U8.1, U8.3, U8.9, U9.3, U10.1, U10.5, U10.7, U10.9, U10.10, U10.11, U10.15, U10.17, U10.19, U10.21, U11.3, U12.3
HELICAL: J2.RF1, U7.8
LNA_DISABLE+3.3V: JP4.1, JP4.3, R29.2, U6.2
LNA_DISABLE_+5.0V: U6.4, U12.2
LNA_ON_OFF: R30.1, R31.1, U4.6, U5.6
unnamed: C28.2, R6.1, R8.1
unnamed: J1.RF1, R1.2, R3.1
unnamed: R5.1, SW1.3
unnamed: R1.1, R2.2
unnamed: SW1.2, U1.1
unnamed: FL2.4, R9.1, R13.1
unnamed: C1.2, U5.2
unnamed: C3.1, L5.1, U5.7
unnamed: C2.2, C4.1, L5.2, R14.1
unnamed: LED1.2, U1.4, U2.1, U3.1
unnamed: R11.2, U2.3
unnamed: C3.2, J4.RF1
unnamed: U1.2, U11.4
unnamed: R12.2, U3.3
unnamed: LED1.1, R32.2
unnamed: L1.1, U10.18
unnamed: R30.2, U12.4
unnamed: C15.1, C16.1, C17.1, C19.1, L1.2, L2.2, R17.1, R20.2
unnamed: C18.1, R19.2, U10.8
unnamed: C21.1, L3.1, U10.12, U10.13, U10.14
unnamed: C22.1, C24.2, R18.1
unnamed: C26.2, U4.2
unnamed: C20.1, C23.1, L3.2
unnamed: C28.1, L4.1, U4.7
unnamed: C27.2, C29.1, L4.2, R23.1
unnamed: R20.1, U10.16
unnamed: L2.1, U10.20
unnamed: C26.1, FL1.4
unnamed: LED2.1, R36.2
unnamed: R18.2, U10.2, U10.3, U10.4
PA_MATCH_OUT: C20.2, U8.4
PA_ON_LNA_OFF: R19.1, U2.6, U10.6, U12.1
PA_PAD_OUT: C24.1, R3.2, R4.1
PA_PAD_OUT1: FL2.1, R6.2, R7.1
PA_PAD_OUT2: C1.1, R9.2, R10.1
RX_IN: FL1.1, U8.8
THROUGH: J6.RF1, J7.RF1
TURNSTILE: J3.RF1, U7.4
TXRX-CTRL: C32.1, R26.2, R27.1, U8.5
TXRX-EN: C33.1, R24.2, R25.1, U8.6
TX_RX_COMMON: U7.2, U8.2
TX_RX_CTL: R26.1, U3.6

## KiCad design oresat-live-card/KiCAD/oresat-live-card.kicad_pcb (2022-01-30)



Board: 4 copper layers, 99.8 x 94.6 mm, 371 parts (99 on the bottom side), 292 nets.

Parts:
C1, C4, C7, C11, C18, C28, C31, C39, C40, C41, C42, C54, C55: 0.1uF; .0603-A
C2, C8, C16, C38, C44: 10uF; .0805-B
C3, C5, C6, C9, C10, C12, C17, C34, C37: 1uF; .0603-A
C13, C14, C36: 22uF; C1210
C15, C21: 100n; .0603-A
C19, C22, C29, C30: 12pF, 50V; .0603-A
C20: GCJ32ER71C226KE01L; C1210
C23: 0.1u; .0603-A
C24, C25: 1nF; .0805-B
C26: 0.1uF; .0805-B
C27, C53, C56: 10uF; .0603-A
C32, C35: 1uF; .0805-B-NOSILK
C33: CL05B104KO5NNNC; .0603-A
C43, C45, C46: CGA2B1X7R1C104K050BC; .0402-B-NOSILK
C47: CGA2B1X7R1C104K050BC; .0402-C-NOSILK
C48: CGA2B2NP01H102J050BA; .0402-B-NOSILK
C49: GCM1885C1H101JA16D; .0402-C-NOSILK
C50: 04025U3R0BAT2A; .0402-C-NOSILK
C51: 04025J1R1PBSTR\500; .0402-C-NOSILK
C52: 04025U1R6BAT2A; .0402-C-NOSILK
C57, C58, C59, C60, C61, C62: 50pF; .0603-A
C63, C64: 20pF; .0603-A
C65: 4.7uF; .0603-A
D1, D6, D7, D8, D9, D10, D11: 150060VS55040; LED-0603
D2, D3, D4, D5: BLUE; LED-0603
FB1, FB2, FB3, FB4: BLM18KG300JH1D; 0603
J1: ORESAT-DEBUG-CONNECTOR-CARD; TE_2-1734592-0
J2, J10: SM06B-SRSS-TB(LF)(SN); CONN_SM06B-SRSS-TB_JST
J4: TFM-120-01-L-D-RA; J-SAMTEC-TFM-120-X1-XXX-D-RA
J5: 2X1_TH_JUMPEP; 2X1
J6: J-MOLEX-SMPM-73300-003X; J-MOLEX-SMPM-073300-003X
J7: DM3BT-DSF-PEJS
J8: FTSH-105-XX-X-DV-K; CON10_2X5_DUK_FTSH
J9: U.FL-R-SMA; U.FL-R-SMT
JP1: JUMPER-SMT_2_NO_SILK; SMT-JUMPER_2_NO_SILK
JP100, JP101, JP104: JUMPER-SMT_2_NC_TRACE_SILK; SMT-JUMPER_2_NC_TRACE_SILK
JP105, JP106, JP107, JP108, JP109: JUMPER-SMT_3_1-NC_TRACE_SILK; SMT-JUMPER_3_1-NC_TRACE_SILK
L1, L2: 6.8u; ECS-MPI4040
L7: 0402DC-1N7XJRU; .0402-C-NOSILK
L8: 0805CS-060XJLC; .0805-C-NOSILK
L9: MLK1005S1N0ST000; .0402-C-NOSILK
L10: Fixed Inductors 1008 10nH Unshld 5% 1.6A 60mOhms; INDC2928X203N
PCB1: ORESAT-CARD-V1.3-GENERIC-1RF-POS1
PCBA1: WF-NP9202WF; WF-NP9202
Q1: MMBT2907; SOT23-BEC
Q2, Q4: PMV45EN2R; SOT23
Q3: DMP2240UDM; SOT23-6
Q5, Q6: DMP3050LVT-7; SOT23-6
R1, R2, R3, R4, R5, R29, R49: 4.7k; .0603-A
R6, R7, R11, R12, R15, R16, R17, R18, R19, R20, R21, R22, R28, R30, R32, R34, R39, R46, R52, R61, R62, R64, R72, R76, R97, R99: 10k; .0603-A
R8: 10K; ARRAY_EXBA-M
R9, R10: EXB-A10P103J; ARRAY_EXBA-M
R13, R36, R44: 1M; .0603-A
R14, R33, R38, R40, R42, R51, R53, R54, R55, R56, R57, R58, R65, R66, R67, R68, R69, R70: RC1005F6653CS; .0603-A
R23: 499; .0603-A
R24, R25, R26: EXB-A10P104J; ARRAY_EXBA-M
R27, R59, R60: DNP; .0603-A
R31: 40.2K; .0603-A
R35, R43: 665k; .0603-A
R37, R45: 330k; .0603-A
R41, R48, R71, R73, R74, R75: 100; .0603-A
R47, R50: 0; .0603-A
R63: 100m; R1206
R77, R79, R89, R91, R93, R95: 22; .0603-A
R78, R83, R90, R92, R94, R96, R100, R101: 15k; .0603-A
R80: ERJ-6GEY0R00V; R0805
R81: ERJ-2RKF1100X; .0402-B-NOSILK
R82: ERJ-3EKF2200V; .0603-C-NOSILK
R84: CRCW04023R30FKED; .0402-C-NOSILK
R85: ERJ-3EKF82R5V; .0603-A
R86: ERJ-3EKF93R1V; .0603-A
R87, R88: ERJ-3EKF41R2V; .0603-A
R98: 1.5k; .0603-A
RT2: TDK NTCG163JX103DT1S; 0603-THERMISTOR-B
TP1, TP5, TP6, TP7, TP8, TP10, TP11, TP13, TP15, TP41, TP42, TP43, TP44, TP45, TP46, TP47, TP48, TP49, TP50, TP51, TP52, TP53, TP54, TP55, TP56, TP57, TP63, TP64, TP65, TP66, TP67, TP68: TEST-POINT; 2MM-TEST-POINT
TP2, TP3, TP4, TP9, TP12, TP14, TP16, TP17, TP18, TP19, TP20, TP22, TP25, TP30, TP31, TP35, TP38, TP39, TP40, TP58, TP59, TP60, TP61, TP62, TP69, TP100, TP101, TP102, TP103, TP104, TP105, TP106, TP107, TP108, TP109, TP110, TP111, TP112, TP114, TP115, TP117, TP118, TP120, TP121, TP122, TP123, TP124, TP125, TP126, TP127, TP128, TP129, TP130, TP131, TP132, TP134, TP135, TP136, TP137, TP138, TP139, TP140, TP141, TP142, TP143, TP144, TP145, TP146, TP148, TP149, TP150, TP151, TP152, TP153, TP154, TP155, TP156, TP157, TP158, TP159, TP160, TP161, TP162, TP164, TP165, TP166, TP167, TP169, TP171, TP172, TP173, TP174, TP175, TP176, TP177, TP178, TP180, TP181, TP183, TP184: TEST-POINT3X4; PAD.03X.04
U1, U18: RCLAMP0504FB; SC70-6
U2: TUSB2046IBVF; QFP80P900X900X160-32N
U3: THGBMJG7C2LBAU8; BGA-153(11.5X13)(EMMC-BA)
U4: SN74LVC1G07DCK; C70(TI-DCK)
U5, U15: TPS62112; S-PVQFN-16
U6: SN74LVC1G32QDBVRQ1; DBV5
U7: OSD3358-512M-BSM; OSD335X-BGA-256
U8: MIC94090YC6-TR; SC-70-6_MCH
U9, U20, U21: TPS2041BQDBVRQ1; DBV5
U10: TLVH431; SOT23-3
U11: TCAN330; SOT23-8_TI-DCN
U12, U13: MIC842LYC5; SC70-5
U14: MAX4211FETE; QFN65P400X400X80-17T210
U16: MAX7310ATE; QFN65P400X400X80-17T210
U17: 25AAXX; SOIC8
U19: TQP9111; QFN50P400X400X102-21N
U$1: 3X1_TH_JUMPER; 3X1
Y1: 24MHz; 5X3.2-4SMD
Y2: ABS07-32.768KHZ-T; CRYSTAL_3.2X1.5
Y3: 6MHz; ECS_ECS-060-18-20BM-JEN-TR

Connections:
1.8V-A: C24.1, C25.1, C26.1, R18.1, TP8.1, TP171.1, U7.A7 (SYS_ADC_1P8V), U7.B7 (VREFP), U7.N13 (PMIC_MUX_IN)
3.3V: C2.1, C3.1, C5.1, C6.1, C8.1, C9.1, C11.1, C15.1, C31.2, C40.2, C65.1, J5.P$1 (1), J7.4 (VDD), J8.1 (VTREF), R1.1, R6.2, R7.2, R8.5 (55), R8.10 (55), R9.5 (55), R9.10 (55), R10.5 (55), R10.10 (55), R20.2, R22.2, R24.5 (55), R24.10 (55), R60.1, R76.2, R97.1, R99.1, TP25.1, U2.3 (VCC), U2.22 (~OVRCUR4), U2.25 (VCC), U2.26 (~EXTMEM), U3.C6 (VDDQ), U3.E6 (VDDIO), U3.F5 (VDDIO), U3.J10 (VDDIO), U3.K9 (VDDIO), U3.M4 (VDDQ), U3.N4 (VDDQ), U3.P3 (VDDQ), U3.P5 (VDDQ), U6.5 (VCC), U7.F6 (SYS_VDD1_3P3V@1), U7.F7 (SYS_VDD1_3P3V@2), U7.G6 (SYS_VDD1_3P3V@3), U7.G7 (SYS_VDD1_3P3V@4), U11.3 (VCC), U17.8 (VCC), U$1.P$1 (1)
3.3VA: C41.1, JP101.1, TP165.1, U7.F8 (SYS_VDD3_3P3V@1), U7.F9 (VDDSHV4), U7.G8 (SYS_VDD3_3P3V@2), U7.G9 (VDDSHV5), U7.H7 (SYS_VDD3_3P3V@3), U7.H8 (SYS_VDD3_3P3V@4), U7.H9 (VDDSHV6), U7.J7 (SYS_VDD3_3P3V@5), U7.J8 (SYS_VDD3_3P3V@6), U7.J9 (VDDSHV1), U7.K8 (SYS_VDD3_3P3V@7), U7.K9 (VDDSHV2), U7.L8 (SYS_VDD3_3P3V@8), U7.L9 (VDDSHV3), U18.5 (VCC)
5V: C1.1, C14.1, C28.1, C36.1, C54.1, L1.2, R62.2, TP49.1, U7.P10 (VIN_AC@1), U7.R10 (VIN_AC@2), U7.T10 (VIN_AC@3), U9.5 (IN), U15.10 (FB), U20.5 (IN), U21.5 (IN)
5V_PA: C20.1, C21.1, L2.2, R11.2, R80.2, TP7.1, U5.10 (FB), U8.4 (VIN)
/Connectors/CAN1_H: J4.33, J4.34, TP184.1
/Connectors/CAN1_L: J4.35, J4.36, TP183.1
/Connectors/N$103: J4.1, J4.2, TP62.1
/Connectors/SPARE1: J4.9, J4.10, TP58.1
/Connectors/SPARE2: J4.7, J4.8, TP59.1
/Connectors/SPARE3: J4.5, J4.6, TP60.1
/Connectors/SPARE4: J4.3, J4.4, TP61.1
/Connectors/~SD: J4.39, J4.40
/OSD3358 PWR, ETC. : SIP A, E, F/N$53: C18.1, JP104.1, TP14.1, TP164.1, U4.5 (VCC), U7.K11 (SYS_RTC_1P8V@1), U7.L11 (SYS_RTC_1P8V@2)
/OSD3358 PWR, ETC. : SIP A, E, F/PMIC_PGOOD: TP110.1, U4.2 (A), U7.N12 (PMIC_PGOOD), U7.P11 (PWRONRSTN)
/OSD3358 USB, JTAG, XTAL, etc : SIP B/OSC0_GND: C19.1, C22.1, U7.N15 (OSC0_GND)
/OSD3358 USB, JTAG, XTAL, etc : SIP B/OSC0_IN: C19.2, R13.2, U7.P16 (OSC0_IN), Y1.1 (X1)
/OSD3358 USB, JTAG, XTAL, etc : SIP B/OSC0_OUT: C22.2, R13.1, U7.N16 (OSC0_OUT), Y1.3 (X2)
/OSD3358 USB, JTAG, XTAL, etc : SIP B/USB_CAM_N: C57.1, J10.5, R77.1, R78.2
/OSD3358 USB, JTAG, XTAL, etc : SIP B/USB_CAM_P: C58.1, J10.4, R79.1, R83.2
/OSD3358 USB, JTAG, XTAL, etc : SIP B/USB_CAM_VBUS: FB3.2, J10.6, TP1.1
/Power/AD0: R57.1, R58.2, R69.2, R70.1, U16.1 (AD0)
/Power/AD1: R55.1, R56.2, R67.2, R68.1, U16.2 (AD1)
/Power/AD2: R53.1, R54.2, R65.2, R66.1, U16.3 (AD2)
/Power/BOOT0: TP51.1, U16.10 (IO5)
/Power/CB-RESET: R39.2, TP54.1, U14.9 (CIN2-), U16.9 (IO4)
/Power/CB_CTRL: Q2.1 (G), Q5.1 (G), R64.1, TP52.1, U14.3 (LE), U14.4 (COUT1), U14.6 (COUT2)
/Power/ON/~OFF: C34.1, Q4.1 (G), R46.2, R49.2, TP50.1, U14.1 (VCC), U16.8 (IO3)
/Power/PB6/SCL: TP67.1, U16.4 (IO0)
/Power/PB7/SDA: TP68.1, U16.5 (IO1)
/Power/PEN-SCL-FILT: Q3.6 (D), R37.2, R65.1, R67.1, R69.1, TP42.1, TP66.1, U16.15 (SCL)
/Power/PEN-SDA-FILT: Q3.4 (D), R45.2, R66.2, R68.2, R70.2, TP41.1, TP65.1, U16.16 (SDA)
/Power/POUT: TP64.1, U14.13 (POUT)
/Power/~FAULT: Q2.3 (D), R32.1, TP45.1, U16.7 (IO2)
/oresat-live-card_6/PA_TOGGLE: R30.1, R81.1, U8.1 (VOUT), U19.6 (IREF1)
/oresat-live-card_6/WIFI_ENABLE: J2.1, R29.2
/oresat-live-card_6/WIFI_STATUS: D10.C, J2.2
CAN2_H: J4.17, J4.18, U11.7 (CANH)
CAN2_L: J4.19, J4.20, U11.6 (CANL)
EEPROM_WP: J1.20 (DEBUG-3), R75.1, TP112.1, U18.6 (I4)
GND: C1.2, C2.2, C3.2, C4.2, C5.2, C6.2, C7.2, C8.2, C9.2, C10.2, C11.2, C12.2, C13.2, C14.2, C15.2, C16.2, C17.2, C18.2, C20.2, C21.2, C23.2, C24.2, C25.2, C26.2, C27.2, C28.2, C31.1, C32.2, C34.2, C35.2, C36.2, C37.2, C38.2, C39.1, C40.1, C41.2, C42.2, C43.2, C44.2, C45.2, C46.2, C47.2, C48.2, C50.2, C52.2, C53.2, C54.2, C55.2, C56.2, C57.2, C58.2, C59.2, C60.2, C61.2, C62.2, C63.2, C64.2, C65.2, D1.C, D2.C, D3.C, D4.C, D5.C, D6.C, D7.C, D8.C, D9.C, D11.C, J1.3 (GND), J1.6 (GND), J1.9 (GND), J1.PAD1 (PAD), J1.PAD2 (PAD), J2.3, J2.7, J2.8 (7), J4.27, J4.28, J4.29, J4.30, J4.31, J4.32, J4.37, J4.38, J6.P$1 (SHIELD3), J6.P$2 (SHIELD2), J6.P$3 (SHIELD1), J6.P$4 (SHIELD), J7.6 (VSS), J7.CGND1 (CGND), J7.CGND2 (CGND), J7.CGND3 (CGND), J7.CGND4 (CGND), J7.CGND5 (CGND), J7.CGND6 (CGND), J7.GND (VSS), J8.3 (GND), J8.5 (GND@2), J8.9 (GNDDET), J9.2, J9.3, J10.3, J10.7, J10.8 (7), JP100.2, L7.1, Q2.2 (S), Q4.2 (S), R14.1, R15.1, R16.1, R17.1, R19.1, R25.5 (55), R25.10 (55), R26.5 (55), R26.10 (55), R33.1, R39.1, R40.1, R42.1, R46.1, R51.1, R54.1, R56.1, R58.1, R59.2, R78.1, R83.1, R85.1, R88.2, R90.1, R92.1, R94.1, R96.1, R100.1, R101.1, RT2.2, U1.2 (GND), U2.7 (GND), U2.27 (TSTPLL/48MCLK), U2.28 (GND), U2.31 (TSTMODE), U3.A6 (VSSIO), U3.C4 (VSSQ), U3.E7 (VSSIO), U3.G5 (VSSIO), U3.H10 (VSSIO), U3.J5 (VSSIO), U3.K8 (VSSIO), U3.N2 (VSSQ), U3.N5 (VSSQ), U3.P4 (VSSQ), U3.P6 (VSSQ), U4.3 (GND), U5.1 (GND), U5.6 (LBO), U5.7 (LBI), U5.9 (GND), U5.11 (GND), U5.12 (GND), U5.16 (GND), U5.PAD (GND), U6.3 (GND), U7.A9 (AGND_ADC), U7.B9 (VREFN), U7.D8 (DGND@1), U7.D9 (DGND@2), U7.E5 (DGND@3), U7.E6 (DGND@4), U7.E7 (DGND@5), U7.E8 (DGND@6), U7.E9 (DGND@7), U7.E10 (DGND@8), U7.E11 (DGND@9), U7.E12 (DGND@10), U7.F5 (DGND@11), U7.F12 (DGND@12), U7.G5 (DGND@13), U7.G12 (DGND@14), U7.H4 (DGND@15), U7.H5 (DGND@16), U7.H12 (DGND@17), U7.H13 (DGND@18), U7.J4 (DGND@19), U7.J5 (DGND@20), U7.J12 (DGND@21), U7.J13 (DGND@22), U7.K5 (DGND@23), U7.K12 (DGND@24), U7.L5 (DGND@25), U7.L12 (DGND@26), U7.M5 (DGND@27), U7.M6 (DGND@28), U7.M7 (DGND@29), U7.M8 (DGND@30), U7.M9 (DGND@31), U7.M10 (DGND@32), U7.M11 (DGND@33), U7.M12 (DGND@34), U7.N8 (DGND@35), U7.N9 (DGND@36), U8.2 (GND_2), U8.5 (GND), U9.2 (GND), U11.2 (GND), U12.2 (GND), U13.2 (GND), U14.7 (GND), U14.EPAD (GND), U15.1 (GND), U15.6 (LBO), U15.7 (LBI), U15.9 (GND), U15.11 (GND), U15.12 (GND), U15.16 (GND), U15.PAD (GND), U16.6 (GND), U16.EPAD (GND), U17.4 (GND), U18.2 (GND), U19.1 (GND), U19.5 (GND), U19.7 (GND), U19.9 (GND), U19.10 (GND), U19.11 (GND), U19.15 (GND), U19.17 (GND), U19.19 (GND), U19.21 (GND), U20.2 (GND), U21.2 (GND), U$1.P$3 (3), Y1.2 (GND), Y1.4 (GND), Y3.2 (GND), Y3.4 (GND)
I2C0_SCL: J1.18 (DEBUG-1), R73.1, TP155.1, U18.3 (I2)
I2C0_SDA: J1.19 (DEBUG-2), R74.1, TP151.1, U18.1 (I1)
unnamed: C10.1, C12.1, U3.C2 (VDDI)
unnamed: C7.1, C27.1, FB3.1, U9.1 (OUT)
unnamed: C29.1, R27.1, U7.A5 (OSC1_OUT), Y2.P$1
unnamed: C29.2, C30.2, U7.B5 (OSC1_GND)
unnamed: C30.1, R27.2, U7.A6 (OSC1_IN), Y2.P$2
unnamed: C32.1, R36.1, R37.1, U12.1 (INP)
unnamed: C33.1, R33.2, R38.2
unnamed: C35.1, R44.1, R45.1, U13.1 (INP)
unnamed: C42.1, C53.1, FB1.1, U20.1 (OUT)
unnamed: C43.1, C45.1, C46.1, C48.1, L8.2, L10.2, R80.1, R82.2
unnamed: C44.1, Q6.6 (D), R63.1, U14.16 (RS+)
unnamed: C47.1, R81.2, U19.8 (IREF2)
unnamed: C49.1, C52.1, L9.2
unnamed: C50.1, L9.1, U19.12 (RFOUT@12), U19.13 (RFOUT@13), U19.14 (RFOUT@14)
unnamed: C51.1, L7.2, R85.2, R86.1
unnamed: C51.2, R84.1
unnamed: C55.1, C56.1, FB4.1, U21.1 (OUT)
unnamed: C63.1, U2.30 (XTAL1), Y3.3 (X1)
unnamed: C64.1, R98.2, Y3.1 (X2)
unnamed: D1.A, R1.2
unnamed: D2.A, R2.2
unnamed: D3.A, R3.2
unnamed: D4.A, R4.2
unnamed: D5.A, R5.2
unnamed: D6.A, R49.1
unnamed: D7.A, R61.1
unnamed: D8.A, R62.1
unnamed: D9.A, R11.1
unnamed: D10.A, R21.2
unnamed: D11.A, R30.2
unnamed: J5.P$2 (2), R16.2, U6.1 (A)
unnamed: J7.1 (DAT2), R8.2 (22), U7.C16 (MMC0_DAT2)
unnamed: J7.2 (DAT3/CS), R8.9 (99), U7.C15 (MMC0_DAT3)
unnamed: J7.3 (CMD/DI), R8.3 (33), U7.B16 (MMC0_CMD)
unnamed: J7.5 (CLK), R8.8 (88), U7.B15 (MMC0_CLK)
unnamed: J7.7 (DAT0/DO), R8.4 (44), U7.A16 (MMC0_DAT0)
unnamed: J7.8 (DAT1), R8.7 (77), U7.A15 (MMC0_DAT1)
unnamed: J7.CD (CD#), R8.6 (66), TP22.1, U7.C14 (SPI0_CS1)
unnamed: J8.2 (SWDIO/TMS), U7.D2 (TMS)
unnamed: J8.4 (SWDCLK/TCK), U7.D1 (TCK)
unnamed: J8.6 (SWO/TDO), U7.C2 (TDO)
unnamed: J8.8 (NC/TDI), U7.C1 (TDI)
unnamed: J8.10 (~RESET), JP1.2
unnamed: J9.1, R86.2, R87.1
unnamed: JP100.1, U7.L14 (USB1_ID)
unnamed: JP101.2, Q1.E, R23.2, R28.2
unnamed: JP104.2, Q1.C, R31.1, U10.3 (ANODE)
unnamed: JP105.1, R24.9 (99)
unnamed: JP105.2, U7.G3 (LCD_DATA0)
unnamed: JP105.3, R25.3 (33)
unnamed: JP106.1, R24.8 (88)
unnamed: JP106.2, U7.G2 (LCD_DATA1)
unnamed: JP106.3, R25.2 (22)
unnamed: JP107.1, R25.1 (11)
unnamed: JP107.2, U7.G1 (LCD_DATA2), U$1.P$2 (2)
unnamed: JP107.3, R24.1 (11)
unnamed: JP108.1, R25.9 (99)
unnamed: JP108.2, U7.H3 (LCD_DATA3)
unnamed: JP108.3, R24.6 (66)
unnamed: JP109.1, R25.6 (66)
unnamed: JP109.2, U7.H2 (LCD_DATA4)
unnamed: JP109.3, R24.7 (77)
unnamed: L1.1, U15.14 (SW), U15.15 (SW)
unnamed: L2.1, U5.14 (SW), U5.15 (SW)
unnamed: L8.1, U19.20 (VCC1)
unnamed: L10.1, U19.18 (VCC2)
unnamed: Q1.B, R23.1, U10.2 (CATHODE)
unnamed: Q3.1 (G), R35.2
unnamed: Q3.2 (S), R41.2
unnamed: Q3.3 (G), R43.2
unnamed: Q3.5 (S), R48.2
unnamed: Q4.3 (D), Q6.1 (G), R52.1
unnamed: Q5.5 (S), R63.2, R64.2, U14.15 (RS-)
unnamed: R2.1, U7.P13 (GPMC_A5)
unnamed: R3.1, U7.T14 (GPMC_A6)
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

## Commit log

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2018-01-04 Fixed Nathan's filter board. Mostly EAGLE stupidity problems. - Switched SMA connectors to the PSAS standard. - Switched grid to 10 mil because OCD. - Loaded OSH Park 2 layer DRC. - Made "RF" class t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
    [BPF_eval.sch, BPF_eval_R2.brd, BPF_eval_R2.sch]
2018-01-04 Cleaned up SPDT switch evaluation board. Same as filter, cleaned up lots of EAGLE stuff. - 10 mil grid, snapped to grid. - Replaced SMA conectors - RF class added. - OSH park 2 layer (4 LAYER?!) DRC 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
    [SPDT_eval.brd, SPDT_eval.sch]
2018-01-04 Switched to OSH Park 4 layer, filled in ground planes on L2. Filter has ground plane on L15, and BPF has VDD on L15.
    [BPF_eval_R2.brd, SPDT_eval.brd]
2018-01-04 Updated RF class to have a 13mil trace width and 13.4mil clearance. Fixed trace widths and moved GND vias closer.
    [BPF_eval_R3.brd, BPF_eval_R3.sch]
2018-01-04 Updated RF class to have 13mil trace width and 13.4mil clearance. I fixed trace widths and moved GND vias closer.
    [SPDT_eval_R2.brd, SPDT_eval_R2.sch]
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2018-08-08 Change to 0402 for some Resistors
    Changed resistors from 0603 to 0402 when electrically OK
    [Bidirectional_Amp.brd, Bidirectional_Amp.sch]
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2018-08-14 minor fixes
    [Bidirectional_Amp.brd]
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2019-01-30 Initial link model
    Antenna gains at 16dBi. Ground station antenna noise temperature is unknown; needs measurement. Transmitters set to 2W. Transmitter and receiver details are estimates. Modulation set to BPSK w/o FEC and data rate at 1Mbps. Uplink barely passes and downlink barely fails.
    [AMSAT-IARU_Link_Model_Rev2.5.5_mod_PDX_CS0_DxWiFi.xlsx]
2019-01-31 Notes fix
    [AMSAT-IARU_Link_Model_Rev2.5.5_mod_PDX_CS0_DxWiFi.xlsx]
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2019-03-27 Added first version of the AR9271 evaluation board. No board layou yet.
    [AR9721_eval.sch]
2019-04-03 AR9721 Brd
    I added my work as of right now on the AR9721. I'm sure there's a large amount of mistakes and I haven't added any RF methods (such as stitching) onto the board.
    [AR9721_eval.brd]
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2019-05-03 Fixed one of many sync errors.
    [AR9721_eval.brd, AR9721_eval.sch]
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2019-05-19 Beginning of OCD cleanup; started with USB lines, worked on RF layout grouping, moved to power planes.
    [AR9721_eval.brd, AR9721_eval.sch]
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2019-05-27 Spelling fix
    [AMSAT-IARU_Link_Model_PDX_CS0_v1_mission_data_uniclogs.xlsx]
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2019-09-11 Handheld link model formatting, minor fixes, update handheld antenna
    [AMSAT-IARU_Link_Model_PDX_CS0_v1_mission_data_handheld.xlsx]
2019-09-14 Add 2nd stage LNAs to SC and GS receivers, and adjust gain.
    [AMSAT-IARU_Link_Model_PDX_CS0_v1_mission_data_handheld.xlsx, AMSAT-IARU_Link_Model_PDX_CS0_v1_mission_data_uniclogs.xlsx]
2019-09-16 First pass of the updated AR9271 dev board. Took Stephen's fine board, and OCD'd it. Still requires stiching, better LAYER3 power layout, TNAMES cleanup, better stiching, but it's close!
    [AR9721_eval.brd, AR9721_eval.sch]
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2019-09-18 Added holes for feet, more stitching, and DRC cleanup. DONE! SHIP IT!
    [AR9721_eval.brd, AR9721_eval.sch]
2019-09-19 Fixed comments on JP4 and moved some names/values around after talking with Glenn.
    [AR9721_eval.sch]
2019-10-25 Added V2 board with separate TX and RX interfaces to WiFi chip
    [Bidirectional_Amp.brd, Bidirectional_Amp.sch]
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2019-11-09 Fixed silk screen based on Jeff's feedback. No change to layout, so same version.
    [AR9721_eval.brd]
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2019-11-17 Check in for Vigely to do some modeling. All routed, but not yet polished.
    [Bidirectional_Amp.brd, Bidirectional_Amp.sch]
2019-11-18 Finished layout! More vias, fixed Vpd issue for LNAs, cleaned up tnames, etc etc.
    [Bidirectional_Amp.brd, Bidirectional_Amp.sch]
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2019-11-19 Fixed trace widths a bit. Should be ready to go.
    [Bidirectional_Amp.brd]
2019-12-01 Made the LNAs the correct part number.
    [Bidirectional_Amp.brd, Bidirectional_Amp.sch]
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2020-03-07 New PA test board, follows better RF practices, new input matching network, and some pointers from Qorvo.
    [Bidirectional_Amp_test.brd, Bidirectional_Amp_test.sch]
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2020-03-11 Fixed filename.
    [AR9271_eval.brd, AR9271_eval.sch, AR9271_eval_BOM.xlsx]
2020-08-22 This is version 2 of PA Test Board. Added stability resistor and changed component values>
    [pa-test-board_BOM.xlsx, pa-test-board_V2.brd, pa-test-board_V2.sch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]
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2020-10-24 copied star tracker card and removed camera stuff to start the oresat live card
    [oresat-live-card.brd, oresat-live-card.sch, pa-test-board_BOM.xlsx]
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2021-01-21 Checking in dxwifi with the latest card outline. but, it's the old v1.0. So it needs to be re-done one more time :(
    [oresat-live-card.brd, oresat-live-card.sch]
2021-01-21 Third time is the charm? Started with Star Tracker v1.2, added new card outline, moved out all extraneaous stuff, added RF connectors.
    [oresat-live-card.brd, oresat-live-card.sch]
2021-01-21 Added and locked DXF layer from Emmy with OreSat live camera mount. Added lens cutout, added TSTOP/TRESTRICT and bottom layers around hardware. Added WF board and 1mm connector. Ready for munging!
    [oresat-live-card.brd, oresat-live-card.sch]
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2021-01-23 Wired debug conector and moved the octavo closer to the front of the card
    [oresat-live-card.brd]
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2021-01-24 reverted impedance matching
    [oresat-live-card.brd]
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2021-01-24 relocated emmc pullups and reworked the assigned pins for easier layout
    [oresat-live-card.brd, oresat-live-card.sch]
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2021-01-25 routed sd data and reworked R8 pinout
    [oresat-live-card.brd, oresat-live-card.sch]
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2021-01-26 fixed incorrect trace widths
    [oresat-live-card.brd]
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2021-01-27 Updated to tuned values, fixed BOM formatting.
    [pa-test-board_BOM.xlsx, pa-test-board_V2.brd, pa-test-board_V2.sch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]
2021-01-29 fixed messed up pull up and down conections on R24 and R25
    [oresat-live-card.brd, oresat-live-card.sch]
2021-01-29 rerouted USB on top layer and conected it to the wifi conector
    [oresat-live-card.brd, oresat-live-card.sch]
2021-01-30 removed R29 and R30 pull ups from the unsed I2C #2 bus
    [oresat-live-card.brd, oresat-live-card.sch]
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2021-01-31 Cute little carrier board for the WF-NP9202 for testing out for DxWiFi.
    [wf-np9202-carrier.brd, wf-np9202-carrier.sch]
2021-02-02 Fixed WF connector pinout
    [oresat-live-card.brd, oresat-live-card.sch]
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2021-02-03 Rearanged the front right to make more room for the WF 5v regulator
    [oresat-live-card.brd, oresat-live-card.sch]
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2021-02-04 routed the 5V supply for the PA and placed it on the board in a temporary spot
    [oresat-live-card.brd, oresat-live-card.sch]
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2021-02-09 Moved the WiFi module to the bottom and rerouted the PA 5V regulator
    [oresat-live-card.brd, oresat-live-card.sch]
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2021-02-11 rerouted some of the boot control lines to make room for length matching the emmc lines
    [oresat-live-card.brd, oresat-live-card.sch]
2021-02-11 added vias to all 3.3v conections for a 3.3v pour on layer 15
    [oresat-live-card.brd]
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2021-02-12 Added the status LED and power toggole resistor for the WiFi module
    [oresat-live-card.brd, oresat-live-card.sch]
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2021-02-15 Added capcitors to the analog power and 1.8V rail, chose AIN6 for the thermistor, changed the thermistor to the 1.8V rail. Routed the listed changes and additions
    [oresat-live-card.brd, oresat-live-card.sch]
2021-02-15 fixed routing errors
    [oresat-live-card.brd]
2021-02-15 Found a missing 1.8V connection for PMIX_MUX_IN
    [oresat-live-card.brd, oresat-live-card.sch]
2021-02-17 moved the PA 5V supply to the top right of the board and routed the PA TX connections
    [oresat-live-card.brd]
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2021-02-18 routed 5V connections and cleaned up airwires and missing ground connections
    [oresat-live-card.brd, oresat-live-card.sch]
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2021-02-19 Added 5V_PA polygon, did some OCD cleanup on RF sheet, yelled at Nick a lot.
    [oresat-live-card.brd, oresat-live-card.sch]
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2021-02-19 modified thermistor routing to not go though vias after it was moved
    [oresat-live-card.brd, oresat-live-card.sch]
2021-02-19 Fixed the I2C0 ESD protection following Oliver R's instructions
    [oresat-live-card.brd, oresat-live-card.sch]
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2021-02-19 Added a 5V polygon. I'm not happy with it and will work on a better colution but it work for now
    [oresat-live-card.brd]
2021-02-20 reworked the 5V and 3.3V polygon routing
    [oresat-live-card.brd, oresat-live-card.sch]
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2021-02-21 fixed minor DRC errors
    [oresat-live-card.brd]
2021-02-21 Added ground vias next to the RF inductors, SMPM connector, and more around the U.FL
    [oresat-live-card.brd, oresat-live-card.sch]
2021-02-21 Clean up with Nick and Oliver: ran ERC, fixed 1.8V-A supply, ran DRC, some layout polishing, added restricts on WF board and moved it down to avoid the SD card, did some thermal polishing for the PA.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
    [oresat-live-card.brd, oresat-live-card.sch]
2021-02-21 Verified all component keepout errors for adequate soldermask clerance and move a few
    [oresat-live-card.brd]
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2021-02-28 changed the oscillator caps to 12pF
    [oresat-live-card.sch]
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2021-03-08 Small fixes; polishing.
    [oresat-live-card.brd, oresat-live-card.sch]
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2021-04-05 Updated board text to v1.1, updated flight hardware marker, fixed eMMC routed through A6 issue
    [oresat-live-card.brd, oresat-live-card.sch]
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2021-04-05 Added tStop along the RF path and shifted the GND vias next to the RF backplane connector into the connectors GND solder pad to match the C3 and GPS
    [oresat-live-card.brd]
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2021-04-09 Adjusted misc silkscreen labels and corrected connector refdes's
    [oresat-live-card.brd, oresat-live-card.sch]
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2021-04-12 Replaced all test points for the PA support circuits with through hole test points
    [oresat-live-card.brd, oresat-live-card.sch]
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2021-04-19 Changed TP1 on the VOUT_USB to a through hole insted of a pad
    [oresat-live-card.brd, oresat-live-card.sch]
2021-04-19 shifted a few test points and their labels to fix overlap issues
    [oresat-live-card.brd]
2021-04-19 Fixed the WF sourcing power from 2 sources and increased all 3.3V and 5V led resistors
    [oresat-live-card.brd, oresat-live-card.sch]
2021-05-16 I'm not really sure, I know I made goof changes but forgot what they were
    [oresat-live-card.sch]
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2021-08-04 added usb hub reset pullup and vcc filter cap
    [oresat-live-card.brd, oresat-live-card.sch]
2021-08-05 reverted changes made over the last couple of days. Removed usb host circuit. Renamed usb client to usb device.
    [oresat-live-card.brd, oresat-live-card.sch]
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2021-08-06 replaced boot and PA_enable jumpres with smaller one, started clearing space for the usb hub
    [oresat-live-card.brd, oresat-live-card.sch]
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2021-08-07 swapped usb host and wifi data line ports on the hub
    [oresat-live-card.brd, oresat-live-card.sch]
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2021-08-08 connected 3.3v to all new usb ic's, corrected many DRC errors and air wires
    [oresat-live-card.brd]
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2021-08-09 Final polish on v1.1.
    - Added pulldowns on unused USB port, added pullup on !OC input for that port.
    - Added TPL/BPL lines for the camera board and lens holder. Moved some parts around to avoid the 33.5 mm OD of the lens holder.
    - TNAMES cleanup
    - Made some traces thicker (don't use TRACE rule for wires if you can help it)
    - Fixed isolate on some layer 15 polygons
    - Cleaned up some traces coming non-orthogonally out of pads.
    - Fixed TUSB and TPL pin directions (in eagle libraries).
    [oresat-live-card.brd, oresat-live-card.sch]
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2021-08-15 replaced usb hub 6MHz crystal with an easily avalible one
    [OreSat Live BOM_R1.xlsx, oresat-live-card.brd, oresat-live-card.sch]
2021-08-15 cleaned up most DRC errors
    [oresat-live-card.brd]
2021-08-15 accidentally overwrote BOM, reverting
    [OreSat Live BOM_R1.xlsx]
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2021-08-24 Updated BOM after stuffing the OL v1.2 cards. Collapsed some resistor values, fixed a few packages, etc.
    [OreSat Live BOM.xlsx, oresat-live-card.brd, oresat-live-card.sch]
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2021-09-04 Decided not to rearange OPD, reverted to 2021-23-08 commit. Started ripping the board appart in functional chunks
    [oresat-live-card.brd, oresat-live-card.sch]
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2022-01-16 reverted board back to v1.1 for KiCad conversion
    [oresat-live-card.brd, oresat-live-card.sch]
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2022-05-09 OreSat Live card V1.2, last silkscreen tweaks and edgecut fixes
    [Connectors.kicad_sch, OSD3358_USB_XTAL_etc.kicad_sch, OSD3358_sysboot.kicad_sch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]
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2022-05-29 Revert "OreSatLive Card v1.2, schematic changes that I totally ment to not push last time I swear that was totally intentional"
    This reverts commit 8d63213ca5702f650b1cf534c3d24906942b58ae.
    [OSD3358_SD_eMMC.kicad_sch, oresat-live-card.kicad_sch]
2022-05-30 Fixes to V1.2
    silkscreen/solder stop cleanup
    ground vias around chasm of doom now actually connected to ground
    mounting drill polygons are now filled
    solderstop closer to S-band transmission line
    soldermask "dams" added to components on S-band signal path
    Weird bug with copper too close to S-band microstrip fixed
    [OSD3358_PWR_ETC.kicad_sch, OSD3358_SD_eMMC.kicad_sch, OSD3358_USB_XTAL_etc.kicad_sch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]
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2022-05-31 Reverted SMPM pocket drills to be outlines
2022-05-31 Reverted mounting and u.fl pass through polygons to outlines instead of filled
2022-05-31 Fixed issue with priority level of ground plane polygon.
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2022-07-06 Fixed schematic error with 5v regulators
    [Connectors.kicad_sch, OSD3358_PWR_ETC.kicad_sch, OSD3358_SD_eMMC.kicad_sch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]
2022-07-12 Fixed 5v regulators
    [Connectors.kicad_sch, OSD3358_PWR_ETC.kicad_sch, OSD3358_SD_eMMC.kicad_sch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]
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2022-07-19 fixed microstrip soldermask pull keepaway
2022-07-19 fixed u.fl pad missing gnd connection
2022-07-19 found cause of thermistor net issue and fixed it (I know I said I fixed it earlier, I lied)
2022-07-20 cleaned up DRC errors
    [oresat-live-card.kicad_sch]
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2022-10-26 replaced smpm footprint, added stitching around smpm
    [Connectors.kicad_sch, OSD3358_SD_eMMC.kicad_sch, Power.kicad_sch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]
2022-10-26 fixed missing camera cutut, fixed stitching, cleaned up remaining warnings
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2022-10-31 reouted forgotten UART, cleanned up DRC. There should be 59 DRC errors caused by the RF frontend and 1 warning caused by the RF front end
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2022-11-21 found value issue with Q5 and Q6 where they do not export to ibom with part number
    [Connectors.kicad_sch, OSD3358_PWR_ETC.kicad_sch, OSD3358_SD_eMMC.kicad_sch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]
2023-12-21 Updated OreSat Live Card. Added changes from the C3 v6 Octavo circuitry and GPS card update. Fixed some GitHub issues. Board layout still in progress.
    [Connectors.kicad_sch, OSD3358_PWR_ETC.kicad_sch, OSD3358_SD_eMMC.kicad_sch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]
2023-12-22 Finished layout, and cleaned up more errors/warnings
    [OSD3358_USB_XTAL_etc.kicad_sch, Power.kicad_sch, RF.kicad_sch]
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2024-01-02 Fixed issue with VPD diodes
    [OSD3358_PWR_ETC.kicad_sch, Power.kicad_sch]
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2024-01-02 Cleaned up ERC and DRC errors on DxWiFi Card
    [Connectors.kicad_sch, OSD3358_PWR_ETC.kicad_sch, OSD3358_SD_eMMC.kicad_sch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]
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2024-07-10 Updated KiCAD import of bidirectional amplifier. Still a bit broken, but better now.
    [Antenna_Select_Switch.kicad_sch, Bidirectional_Amp.kicad_pcb, Bidirectional_Amp.kicad_sch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]
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2024-07-16 Annotated schematic and added/fixed attributes
    [receive_Path.kicad_sch]
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2024-07-28 replaced symbol for connector with 3-pin symbol
    [receive_Path.kicad_pcb, receive_Path.kicad_sch]
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2024-09-05 fixed connector reference designators and BOM for receive test board
    [receive_Path.kicad_pcb, receive_Path.kicad_sch]
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2024-09-19 added missing DPN and MPN, fixed silkscreen labels
    [receive_Path.kicad_pcb, receive_Path.kicad_sch]
2024-11-06 Imported Oresat KiCAD 4 layer board prefs, including GND backoff on RF netclass. Fixed a few minor DRC warnings.
    [receive_Path.kicad_pcb]
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2025-04-26 added missing RF swtich
    [LNA.kicad_sch, TX_RX_SWITCHING.kicad_sch]
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2025-05-10 implemented notes from Oliver. Added notes for self to fix later
    [ANTENNA_SWITCH.kicad_sch, Connectors.kicad_sch, LNA.kicad_sch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]
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2025-07-02 Fixed up schematic as best as possible. There were a lot of issues with local paths being referenced, and EAGLE import libraries. Fixed all of those, as well as fixed some oresat-kicad IC symbols (ba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
    [ANTENNA_SWITCH.kicad_sch, Connectors.kicad_sch, LNA.kicad_sch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]
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2025-07-06 fixed USB hub symbol to be filled
    [OSD3358_USB_XTAL_etc.kicad_sch]
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2025-08-05 swapped placement of R105 and R88, changed R109 from 100 to 56 ohms, relabelled PWR_DET_OUT to RX_DET_OUT, added inverter to TX/RX Control switch and swapped RF1 and RF2
    [LNA.kicad_sch, OSD3358_USB_XTAL_etc.kicad_sch, PA.kicad_sch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]
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2025-09-08 Cleared out most DRC errors, added teardrops & curves to RF nets, minor schematic changes
    [LNA.kicad_sch, OSD3358_SD_eMMC.kicad_sch, PA.kicad_sch]
2025-09-17 Fixed schematic symbolrs, add notes about control logic, fixed RF path and teardrops, removed 1.1V power LED
    [Connectors.kicad_sch, LNA.kicad_sch, OSD3358_PWR_ETC.kicad_sch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]
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2025-09-17 Fixed ERC and schematic-board consistency issues, including some library elements.
    [oresat-live-card-sch-sip-b.kicad_sch, oresat-live-card-sch-wifi-lna.kicad_sch, oresat-live-card-sch-wifi-switch.kicad_sch]
2025-09-17 Updated OPD / power page and synced with CFC processor, fixed layout issues.
    [oresat-live-card-sch-connectors.kicad_sch, oresat-live-card-sch-power.kicad_sch]
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2025-09-17 Schematic cleaned up and should be good to go. Lots of DRC errors to fix. Also waiting for design review.
    [oresat-live-card-sch-sip-a.kicad_sch, oresat-live-card-sch-sip-b.kicad_sch, oresat-live-card-sch-sip-c.kicad_sch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]
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2025-09-22 Clean up DRC errors, thermistor routing clenup
    [oresat-live-card-sch-power.kicad_sch]
2025-09-22 Moved WiFi switch to 5VA, making the entire RF subsystem powered off that one supply. Fixed up RF path, still need to remove solder mask.
    [oresat-live-card-sch-wifi-switch.kicad_sch]
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

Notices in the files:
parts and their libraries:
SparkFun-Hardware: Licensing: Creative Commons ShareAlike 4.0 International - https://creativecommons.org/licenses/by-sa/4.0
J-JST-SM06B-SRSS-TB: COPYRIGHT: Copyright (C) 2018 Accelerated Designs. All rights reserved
